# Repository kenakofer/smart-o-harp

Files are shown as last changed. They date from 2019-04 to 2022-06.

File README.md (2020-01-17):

## Summary

This site details an ongoing project to improve the chord selection mechanism on chromatic Autoharps/Chromaharps (hereafter called just "autoharps"). An arduino reads inputs from a keypad, computes the desired chord from the keypresses, and mechanically dampens the undesired strings.

It does **not** strum or pluck for the human, nor does it change chords without human input.

See [Motivations](#motivation) for why this project is useful.

See [Dampening Mechanism](#dampening-mechanism) for an for detailed analysis of dampening mechanism possibilities.

See [Avoiding harmonic nodes](#avoiding-harmonic-nodes) on the importance of considering harmonics when experimenting.

See [Keypad → Notes logic](#keypad--notes-logic) for more discussion than you wanted about sensible chord setups.

See [Wiring and Components](#wiring-and-components) to see how and with what it can be constructed.

--------

## Motivation
#### Autoharps are limited in number/variety of chords

Most autoharps have between 12 and 21 chord bars, with the ability to play in only some of the 12 musical keys. The chords available are usually major chords, minor chords, major-minor 7 chords, and sometimes a diminished chord.

Thinking just about these 4 types of chords, the maximal manual autoharp can play 21 of them, out of the `12*4=48` possible.

Stepping out of the chord bar paradigm can allow more flexibility.

#### Ergonomics of chord layouts can only go so far, and are not always key agnostic

The best layout I've found with 21 bars is to have each column be of the form (from farthest reach with the left hard to closest): `(Am, C, A7)`. Successive columns just walk this around the circle of fifths. This makes playing most major and minor songs in 5 key signatures ergonomic and *key agnostic* (transposing a song is as simple as shifting your chording hand over). Still, one of several flaws with this layout: When one wants the major/minor version of the minor/major chord, it's a wide reach that may go off the harp.

Stepping out of the 1 button = 1 chord paradigm can allow more flexibility.

#### Playing autoharps for long periods can cause cramping, arthritis, or other joint pain in the chording hand.

Depending on how well tuned the harp is and how the hand is positioned, this may be more or less of an issue. I don't play for more than an hour at a time, due to cramping.

Stepping out of the finger-force dampening paradigm etc.

----------

## Dampening mechanism

3 possibilities for this:

#### One solenoid per string

This is my current pursuit. Every string has a small solenoid positioned so that the unpowered state is dampening the string. When powered, the dampener lifts up, allowing that string to sound. The arduino controls the 30-40 solenoids individually, allowing more flexibility than the other two solutions. Cheap solenoids will cost around $1. The batteries I've tried cannot deliver the amps needed, so I'm trying a 12V, 5A laptop charger for now.

**Construction summary**: From a autoharp with exposed chord bars. Remove all bars except for one. Stretch the springs holding that bar so that the bar stays high under more force. Super glue solenoids to the sides of the bar such that the solenoids head is just short of touching the string it should dampen. Padding can then be glued to the head of the solenoid so that the resting state dampens the string effectively. Alternate placing solenoids on each side of the bar to give them enough lateral space.

**Considerations**: Size, shape, material of the dampening pads. Force of dampening. Lower notes' pads need more contact with the string to effectively dampen.

**Pros**: String by string flexibility for chord building, simple construction

**Cons**: Raised solenoids (undampened strings) draw current while remaining raised (one of my tiny $1 solenoids needs at least 70 mA to start lifting, and will continue to draw that while raised).

**Edit 01/13/2020**: On the second build iteration, I found solutions to the energy usage issues.

First, using a [voltage regulator](https://www.amazon.com/DROK-Converter-5-3V-32V-Regulator-Transformer/dp/B078Q1624B/), I was able to reduce the voltage to 9.5 or 10 volts, which reduces current through each solenoid. Each solenoid now needs about 140mA to raise.

Second, one of the solenoids only needs a tiny fraction of that power to stay raised, so the arduino can regulate down the power after a short time, greatly reducing energy costs.

This was a big problem to solve: It makes the prospect of raising all solenoids at once manageable, battery solutions are far more feasible, and the solenoids and components don't get super hot anymore!

#### Depress single-note bars with motor push

This is the second simplest solution. There are 12 "chord" bars, but their felts are cut so that one dampens only the `C`s, one dampens only the `C#`s, etc. Now to form an arbitrary chord, press down the set of bars that correspond to the pitch classes you **don't** want in the chord. Each depression will probably require more force than small solenoids can probably supply, so higher torque stepper motors may be better.

**Construction summary**: From an autoharp with exposed chord bars, take 12 bars and cut their felts to only dampen one pitch class. Replace them in a way to avoid damping on harmonic nodes. Get 12 high torque stepper motors with arms that swivel to straight down (to depress a bar). Mount them above the bars somehow, taking into account their difficult dimensions and the point of downward force on the bar relative to the strings being dampened. Given my lack of construction experience, this last task was too daunting for me.

**Considerations**: Force of dampening. Avoiding harmonic nodes.

**Pros**: Minimal power usage when not changing chords. May be cheaper than the solenoids if done effectively.

**Cons**: Complicated mounting that occupies space in front of chord bars, which may get in the way of the strumming hand.

#### Depress single-note bars with down pulling strings

I only mention this because I seriously tried making it work for a bit. Wouldn't recommend it.

Like the above in terms of the single note bars. For each bar: Tie a string to each end, run it straight downward and around a pivot point, then pull on both ends to depress the bar. Use a motor head to pull the strings taut to dampen a note.

**Considerations**: Allowing the motors to do no work when not changing chords. Motors need to have some torque.

**Pros**: The complicated mounting of the previous can be relocated somewhere less invasive (inside the autoharp body would be really interesting.

**Cons**: Starting to get quite complicated.

--------

## Avoiding harmonic nodes

See the [Wikipedia article](https://en.wikipedia.org/wiki/Harmonic) if you don't know what a harmonic node is. To experience it, place your finger or an eraser exactly halfway along a string, and pluck the string. An octave above the string's note will resonate. Slide along the string to find other points where the string will still sound.

That point on the string is a harmonic node, and is a poor location for a felt to dampen sound. There are other harmonic nodes at `(1/3, 2/3, 1/4, 3/4, 1/5, 2/5, ...)` etc. (all the rational numbers between 0 and 1). As the denominator gets bigger, it matters less in this context.

Whenever we mess with positions of bars and felts on the autoharp, we need to keep this consideration a priority to minimize extraneous noise while strumming. Consider marking all the harmonic nodes on the strings (e.g. with a red marker) before deciding on bar/felt placements that avoid those spots.

-------------

## Keypad &rarr; Notes logic

***Edit 01/13/2020***: If you don't care about motivations and thought processes, skip all this (very interesting) stuff past self wrote. I'll cover my current favorite keypad layout in [On Second Construction](#on-second-construction). That said, I still basically agree with all of this, past self just overlooked a few possibilities and didn't have enough buttons to press.

This project has the opportunity for a very consistent, learnable, ergonomic, key agnostic chord control mechanism. Optimizing for all these is a real puzzle, and different musicians will have different opinions and desires in this area.

Thankfully, the code on the arduino is far more easily changed than the mechanics of the construction, so we don't have to build a new autoharp if we forget a chord.

In this section, there will be tension between 1) incorporating more buttons/controls/physical complexity into the design, so that the amount of interaction needed to change to arbitrary chords is minimized, and 2) having fewer buttons/controls, so that the size/cost/physical complexity is minimized, but more interaction is needed to specify arbitrary chords. Each person probably has their own balance, but I lean more toward the fewer buttons/controls because I'm bad at electronics.

#### Music Theory Considerations for important triads

In a major key, here are the roman numeral chords I want easy access to, in decreasing order of importance: `(I, V(7), IV, vi, ii, II(7), iii, III(7), vii°, VI, VIIb, ...)`  I have high uncertainty after halfway through that list.

Similarly, in a minor key (using the roman numeral `vi` as the tonic chord for consistency): `(vi, iii, III(7), ii, V(7), I, IV, ...)` I have high enough uncertainty that I won't try to add more.

Songs with the richest harmonies have both minor and major progressions in them, so it behooves us to not only make the system key agnostic, but also *tonality agnostic* (a term I just made up: a song that starts major and then goes minor or vice versa shouldn't throw us for a loop).

The first 7 elements of each list have 6 in common, which (probably due to some arcane property of (meta-)music-theory) are also six-in-a-row around the circle of fifths: `(IV, I, V, ii, vi, iii)`.

Or, arranging them in rows as autoharpists typically do:

| | | |
| --- | --- | --- |
| IV  | I | V |
| ii  | vi  | iii |

This seems like an optimal arrangement of 6 buttons for playing diatonically, to be key and tonality agnostic. I'll treat these 6 chords as the core chords, which should be accessible through a single button press.

To actually make it key agnostic though, there needs to be a way to play in more than one key.

**Fixed chord root buttons**: We could do this with static buttons by having 24 buttons that we could arrange in 2 literal circles of fifths. The circles could be one inside the other, and then we literally have a circle of fifths as a control board:

major minor circle of fifths

24 buttons feels like a lot, but it gives us every major/minor triad, and it could make for a really attractive circular keypad, which could rotate to "switch" keys, and have modifier keys inside or outside the main circle. You would have to construct this yourself, as I can't find such a circular keypad online, even just for one row.

If your thumb is used to joysticks, another idea is to map the sectors of a joystick's movement to the circle of fifths. The lack of tactile feedback on the boundaries between chords, or the small 30&deg; sectors might be issues.

**Dynamic chord root buttons**: We can try to use program state to do it with fewer buttons: 6 buttons could code for `(IV, I, V, ii, vi, iii)` as in the table above, and 2 buttons could be used to change our key. Each button can change the key one direction or another around the circle of fifths. This has the disadvantage of not being able to jump to some arbitrary chord root outside the key: `VIIb` and `VIb` come to mind as somewhat common examples. And the chord `vii°` is entirely in the key and we can't reach it either.

The biggest problem is that the II and III chords aren't there. Adding another row can fix that, and also gives us all of the first 7 most important chords in major and minor from above:

| | | |
| --- | --- | --- |
| IV  | I | V |
| ii  | vi  | iii |
| II  | VI  | III |

This third row looks a little redundant next to the second row; especially if the "Swapping major/minor triad" modifier below is convenient to use.

#### Music Theory considerations for chord modifiers

We can expand the possibilities of these chords with modifiers. A modifier is a way to add or modify the notes in the 24 basic triads. Ideally, several modifiers could be added to one triad without much hassle. Each player will probably have a different preference for how these are arranged and which are included, or may even desire to change layouts between songs.

Here's my list of modifiers in decreasing order of importance and increasing order of my excitement: Adding a minor seventh, switching major/minor to minor/major triad respectively, diminishing the chord, sus4-ing the chord (!!), adding a major seventh to the chord (!!!), augmenting the chord (!!!!). There could be add2, add6, 9, 11, 13 stuff as well.

**Adding sevenths**: The major point of contention with having a `+7` modifier button is whether that 7 should be major or minor or context dependent. Chords with a major 7th above the root are rare, and seldom used outside of jazz. [Mechanical autoharps aren't great for jazz](http://jazzmando.com/new/archives/001511.shtml) (Only view if you aren't easily offended), and the possibility for major sevenths would help.

It isn't usually possible to predict the presence of major sevenths from the key signature, and chord sheets are explicit about when the 7 is major: `FM7` or `Fmaj7`. For this reason, it seems most best to use two separate modifiers: A `+min7` button that is in very easy reach for frequent use, and a `+maj7` button if the player wants it.

Alternatively, consider that a single button could be double tapped to get a different behavior, e.g. `+7` once for `+min7` and twice for `+maj7`.

**Swapping major/minor triads**: A `ii` becomes a `II`. A `iii` becomes a `III`. A common progression at the end of songs: `(I - iv - I)`. The `IV` and `V` in a major key get swapped out with their parallel minor counterparts for a more edgy harmony. The [Picardy third](https://en.wikipedia.org/wiki/Picardy_third) makes the last chord of a minor song (un)expectedly major.

Though a minor button and a major button separately are simpler to understand, the minor button would only be useful on major chords, and the major button only on minor chords. Combining them into a single button saves a button for something else.

**Diminished chords**: Three chords of interest: a [diminished triad](https://en.wikipedia.org/wiki/Diminished_triad) (3 notes with minor thirds between them), [fully diminished seventh chord] (https://en.wikipedia.org/wiki/Diminished_seventh_chord) (4 notes with minor thirds between them), and [half-diminished seventh chord](https://en.wikipedia.org/wiki/Half-diminished_seventh_chord) (a diminished triad with a minor seventh on top). The logic I've used thus far does not fit diminished chords well: We don't have `vii°` the most common diminished triad in our base triads; if we did, we still don't have a modifier to add a minor sixth to the chord for the fully diminished seventh. The most comprehensible solution is simply to add a modifier for each variation.

There are a few inelegant hacks we can use if we don't want to add so many buttons for these relatively rare chords. We could add one modifier button, a `dim` button, but have the button work in coordination with our `V` triad to produce the `vii°`. Why `V`? The diminished triad has a (dominant function)[https://en.wikipedia.org/wiki/Dominant_(music)] just like the `V`, and a `V7` can be thought of as a `vii°` with an added fifth scale degree.

We can co-opt other buttons that will not be much use in diminished chords, such as the `+maj7`, to be a `+min6` for the fully diminished chord. We can use the `+min7` as is to produce a half-diminished chord. Each of these chords would require 3 button presses: the `V`, the `dim`, and whichever `+7` button.

**Augmented chords**: These are a piece of proverbial cake relative to the diminished chords. An [augmented triad](https://en.wikipedia.org/wiki/Augmented_triad) is 3 notes separated by major thirds. Ignoring enharmonics (as I do) there are only 3 different augmented chords. So throw on an `aug` button, hit it with `I` or `iii` and you'll get the same effect. The `+7` modifiers are still there if you want to play a really exotic chord.

**Sus4 chords**: In a [sus4 chord](https://en.wikipedia.org/wiki/Suspended_chord) the 3rd is removed and a perfect 4th added. Pretty straightforward unless you want to hack together a more general system to get `sus2` without extra buttons, but I'm cool with just a `sus4` for now.

**You get the idea**: Other modifier ideas: removing the third to make open fifths, removing third and fifth to make octaves (yawn). "Scale" modifiers could be used for allowing playing any notes inside the scale by damping the ones outside the scale. Diatonic scale, pentatonic scale, various minor scales, or other less common scales.

#### Misc. operator buttons

**Left/Right around the circle of fifths**: 2 buttons, `mod5` and `mod4` to allow the instrument to change keys in two directions: `V` becomes `I`; and `IV` becomes `I`. Modulating by minor thirds might also be useful to go quickly between parallel major/minor keys.

**Previous chord**: There are frequently times when you are walking a melody up a scale and have to go back and forth between passing chords. Having a `prev` button to go to the chord just before the one currently playing could save 1 or 2 key presses depending on how complicated the chords are.

#### Keypress timing considerations

Timing is very important and has not yet been discussed. Some keypads do not support detecting multiple keys pressed at the same time, so combinations of keys pressed to produce a chord cannot happen at once. We will call this a _sequential_ keypad system. Many more keypads have, at least in their hardware, the ability to correctly detect certain simultaneous keypresses, but not others. We'll call a system that can detect some number of simultaneous keypresses correctly a _simultaneous_ keypad system. We'll start with thinking sequentially for simplicity's sake.

#### Sequential principles

Most of the time when you press the `IV` button, you just want to play that chord as is. But suppose one time in the middle of a song it's a minor `iv` chord, requiring the major/minor modifier plus the `IV` button. Thinking sequentially, one button press has to come before the other.

If the `IV` is first, the arduino can either 1) wait for more input, or 2) immediately make the chord available with possibly the wrong tonality.

If the `maj/min` is first, the arduino can either 3) wait for more input, or 4) immediately change the current chord to the opposite tonality.

Of these 4 scenarios, I like 3 best. Immediate changes mean the instrument will be in states of the wrong tonality. If the arduino is to wait for something, it's best that the "something" be definite. We've talked about the 6 fundamental triad controls, and one reason they are so fundamental is that they are the common element, and thus can safely be the element that actuates the changing of the chords in one quick motion.

Say we're in C major, and we want to play `E7`, which is `III7`. So the order of the sequential presses would be `maj/min`, `+m7`, `iii`. Only pressing the final button would cause the dampened strings to change. Not gonna lie: this sounds painful given how often I use `III7`.

#### Sequential layout ideas

Given the above, here are some of my ideas for "good" sequential keypad layouts. Any of these could have part or all of it rotated 90&deg; to better fit under the fingers.

**12 button sequential keypad A (fast and simple):**

| | | |
| --- | --- | --- |
| IV  | I | V |
| ii  | vi  | iii |
| II7 | VI7 | III7|
| mod4|+min7| mod5|

This layout should play melodies quickly and efficiently. The presence of the third triad row (with 7s already added because of their nearly universal use on secondary dominants) allows us to leave out `maj/min` modifier. We can play most chords with a single keypress, with the exception of the `V7` (this is a real downer). Even with just these 12 buttons, the player can play in all 12 key signatures, major and minor, with the most common chords, have minor chords with minor sevenths, major sevenths if you use a double-tap logic, and modulate keys mid song without fuss. 

Some players might like swapping out the `+min7` for a `V7` button, or have the double tap behavior provide the `V7`, or some variation on that.

**12 button sequential keypad B (slower and deeper):**

| | | |
| --- | --- | --- |
| IV  | I | V |
| ii  | vi  | iii |
|+min7|maj/min|sus4|
| mod4|prev | mod5|

We remove our convenience row of chords to add more cool modifiers to show off with. Double taps would open open up more possibilities `+min7`  &rarr; `+maj7`; `maj/min` &rarr; `dim`; `sus4`  &rarr; `sus2`. But here the secondary dominants with sevenths require 3 presses. This could be fine for chording and slower melodies, but not faster ones. The `prev` button recovers some speed between alternating chords.

#### Simultaneous principles in row, column keypads

The possibility of pressing multiple keys at the same time allows for faster fingering of chords with modifiers, but introduces complexities of hardware and timing. For a better introduction to these issues on a typical computer keyboard, [see here](https://en.wikipedia.org/wiki/Rollover_(key)).

**No ground pin**: It's common for keypads to be wired such that each row and column corresponds to a pin, such that pressing the button in the first row and first column connects the first row pin (`row1`) to the first column pin (`col1`). Suppose that the button in the first row, second column is also pressed. then `row1`, `col1`, and `col2` are all connected to each other.

Keypad backside wiring

But the arduino's logic is in reverse: (Ex. 1) If it sees that `row2`, `col3`, and `col4` are connected to each other, can it know for certain what buttons are pressed? In this case, yes, because a button press is always at the intersection of a row and column, and a row or column pin can't be in the connected list without having a pressed button. We can extend this logic to say that any number of keypresses in any single row or in any single column are always safely distinguishable.

(Ex. 2) If `row1` and `col1` are connected, and `row2` and `col2` are separately connected, the arduino still knows the exact two buttons that are pressed. This, along with the first example, shows that any two simultaneous keypresses are distinguishable.

Certain combinations of 3 simultaneous keypresses introduce ambiguity. (Ex. 3) If ever there is a pressed button (e.g. `row1, col1`) who has another pressed button buddy in their row (`row1, col2`), and also a pressed button buddy in their column (`row2, col1`), then all the arduino sees is a group of 4 connected pins: `row1`, `row2`, `col1`, `col2`. Some combination of 3 or 4 of these were pressed, but there's no way to know which. 

However, ambiguity is not necessarily a deal-breaker: as long as the arduino has a sensible default for how to interpret specific situations of ambiguity, it can use that default. We just want to avoid designing a system that allows two useful "button signatures" to have the same "pin signature" from the arduino's perspective.

**With ground pin**: My keypad is weird in that it has a pin that connects to every button, which I'll call the `ground`. So pressing the top left button connects `row1`, `col1`, and `ground`. So Ex. 2 isn't a possibility, because all button presses connect the entire set of row and column pins involved. So the only unambiguous button presses are, as descibed in Ex. 1, within a single column or within a single row. The same note about ambiguity applies.

I'm honestly not sure where I got this keypad, or why I would want this `ground` pin when it seems to only decrease the functionality.

**Regardless**, it is safe for us to make plans for simultaneous keypresses in a single row or column. This limitation still allows quite a few possibilities, but makes simultaneous modifier keys, like a `+min7` difficult to put somewhere that is usable by all the relevant chords. As a result, I'll try to avoid having modifier keys at all.

**12 button simultaneous keypad (Bear With Me edition):**

This will get kind of complicated to diagram now. It's better to have lots of choices IMHO, but I realize many will disagree with me. Note that "2 buttons to the left" will sometimes mean wrapping back around to the right side.

**Interpretation:** Default chord (chord when button to the left is also pressed) (chord when the 2 buttons to the left are both pressed)

| | | | |
| --- | --- | --- | --- |
|  VIIb (vii°) (vii°7) | IV (IV7) (IVmaj7) | I (I7) (Imaj7)  | V (V7) (Vmaj7) |
| v (iv) (i)  | ii (II7) (ii7) | vi (VI7) (vi7) | iii (III7) (iii7) |
| mod4 | prev | +sus4 | mod5 |

First off, I sincerely apologize for the first column, you may ignore it as you are picking up the pattern of the rest of the table. 

Pressing a bunch of buttons in a row are interpreted as a modifier on the rightmost of the buttons pressed (wrapping from left to right is important, e.g. to get the `vii°` one would press `VIIb` and `V`). This mostly serves to add various sevenths to chords, and differs between the major and minor triads.

**Major**: When 1 button to the left is pressed, it does `+min7`. When 2 buttons are pressed, it `+maj7`s the chord.

**Minor**: When 1 button to the left is pressed, it majors it and does `+min7`. When 2 buttons are pressed, it just `+min7`s the chord. I didn't use `+maj7` because that isn't as much used on minor chords.

And the first column just throws in all the things I would be sad not to have, in a vaguely circle-of-fifths-y way. This layout throws easy comprehension out the window in favor of packing in the options in an ergonomic manner (Imagine alternating between fingerings for `I` and `V7`, just by lifting a single finger, or doing the same between `III7` and `vi`).

Note that on a grounded pin keypad, the `+sus4` introduces ambiguity when pressed simultaneously with, say, `V`. It connects pins `row3`, `col3`, `row1`, and `col4`. However, if we are content with only using `+sus4` with a single other button press, and not using the other buttons in the 3rd row with the triad buttons, we can have the arduino interpret this ambiguity predictably as using the `+sus4` with whichever button is diagonal to it. No-ground-pin keypads don't need to worry about this.

I'm not sure how useful the `prev` button will be in this layout, because most back-and-forth passing chords are pretty easy to go between already. I add it here mostly because I don't know what else to put in that space. I can't have another typical modifier due to the paragraph above. I could have a parallel minor modifier that is only used with the `mod4` and `mod5` buttons to change key up or down by a minor 3rd easily. Or I could put another chord there, like the `VIb`.

## On Second Construction

This section is written much later. On the second construction attempt, I solved a lot of major issues.

I started over building because the first build was cludgy and bad in its
unfinished state. Here are the major changes in the second construction, in
the software:

 - Using 16 button keypad (4 column, 4 row pins, no weird ground pin
 this time ;) This allows:
 - Different button reading strategy: Use two dimensional array of
 button states rather than row and column states. This allows a lot more
 keypresses without ambiguity.
 - Keymapping to chords substantially rethought. Now it doesn't use ANY
 simultaneous keypresses, but considers some keys as "modifiers" which
 don't do anything when pressed on their own, and "actuators" (maybe
 find better name?) which when pressed immediately actuate a chord with
 whatever modifiers are down. See the big comment in the code for the
 layout.
 - The above means that we were able to get rid of the `buffer_chord`
 system entirely! :celebrate:
 - Chords can now have up to 5 notes to allow for things like Dominant 9
 chords. No reason it couldn't be more.
 - Major power reduction by using pin 10 on the arduino to change
 current flowing to the solenoids. The solenoids need lots more power to
 pop up than they need to stay up, so every chord change starts at
 `FULL_POWER` then drops power usage considerably to `LOW_POWER` after
 `TICKS_AT_FULL_POWER` ticks.
 - Pasted in the function `setPwmFrequency` to use on pin 10, because
 the default, slower frequencies cause audible hums during `LOW_POWER`

Major changes in the hardware that weren't mentioned in the software:

 - I'm now soldering female header pin connectors rather than the components themselves into the soldering board. If I fry another Arduino Nano or break a keypad it will be a trivial swap-out rather than a solder-mess project-killer.
 - Similarly, on each solenoid, I'm putting a jumper cable head on one of the wires. This way, it can be plugged in rather than soldered in. Same logic as above, and flexibility of rewiring on the fly if the autoharp strings are tuned to different pitches.
 - I'm now using a [voltage regulator](https://www.amazon.com/DROK-Converter-5-3V-32V-Regulator-Transformer/dp/B078Q1624B/), which helps me fiddle with and monitor power better. It might not be necessary in the long run, but for a prototype it is _incredibly_ handy to simply bump the voltage up or down.
 - I'm not trying to incororate LEDs this time around. Simpler design, more in my pay grade.

### Most recent keypad layout (4x4 buttons)

My new keypad's hardware doesn't have ambiguity unless 3 or more button presses are at the corners of a rectangular area. This allows some clever setup of held (not simultaneous press!) modifier keys. Getting rid of simultinaety is huge I think.

**Single press with single modifier**

| | | | |
| --- | --- | --- | --- |
| VIIb | IV | I | V |
| ii | vi | iii | vii° |
| _Make Do_ | _Sus2_ | _Sus4_ | _Maj/Min_ |
| _mM7_ | _MM7_ | _mm7_ | _Mm7_ |

**Single press with double modifier in vertical stacks**

| | | | |
| --- | --- | --- | --- |
| VIIb | IV | I | V |
| ii | vi | iii | vii° |
| _Dim_ | _Aug_ | _Dim7_ | _1/2 Dim 7_ |
| _(^^^)_ | _(^^^)_ | _(^^^)_ | _(^^^)_ |

Note that:

 - The arrows _(^^^)_ mean that both modifiers must be pressed for the listed modifier to apply. Still, nothing will actuate until a chord button is pressed.
 - Because these modifiers are vertically stacked, it is impossible for a single chord button to form a rectangular area, so hardware ambiguity is avoided.

**Single press with double modifier in diagonal combinations**

| | | | |
| --- | --- | --- | --- |
| VIIb | IV | I | V |
| ii | vi | iii | vii° |
| | | _Dom9_ | |
|  |  |  | _(Dom9)_ |

Note that:

 - I'm not sure how well these combos will work ergonomically, so I'm only trying one for now. _Dom9_ means Root, M3, P5, m7, M9(M2).
 - Once again, these diagonal combinations avoid hardware ambiguity when one of the chord buttons is pressed

**Horizontal Double modifier as chord button:**

| | | | |
| --- | --- | --- | --- |
| VIIb | IV | I | V |
| ii | vi | iii | vii° |
| | | VIb | (<<<) |
|  |  | IIIb | (<<<) |

 - These horizontally aligned modifiers would NOT work unambiguously with all chord buttons (If the `I` were pressed, it would look like `V` was also pressed), so it seems reasonable to actually make the modifiers actuate in combination with each other. This means that these particular chords can't have modifiers applied to them to make, for example, a VIb seventh chord.
 - Not all slots are used, because most other chords we really want to be able to add other modifiers

 I'll update the Wiring and Components section at some point, it's outdated for now

--------

## Outdated Wiring and Components

3 main topics here, which others have covered pretty well already so I don't need to. Click the links to read more.

1. [8-bit shift registers](https://www.arduino.cc/en/tutorial/ShiftOut): Getting the (at least) 12 outputs necessary to control 12 systems of solenoids independently, without using up all the arduino's pins.

2. [Driving solenoids with an arduino](https://core-electronics.com.au/tutorials/solenoid-control-with-arduino.html): Except that we will drive the solenoids and the arduino off the same power source, so maybe this isn't super relevant.

3. [Keypad input method](https://www.instructables.com/id/Arduino-Button-Tutorial/): having the arduino read in button presses. This is basic input/output stuff, and the linked tutorial is excellent for looking at a single case. I've covered the specific convoluted logic of my keypad already.

Here's my breadboard setup all laid out. This is diagram version 2, using the nano and fixing some wire placement issues from the first version. 

**Disclaimer**: I'm not great at electronics as I write this. I fried several components on my way to what I hope is a safe, working design.

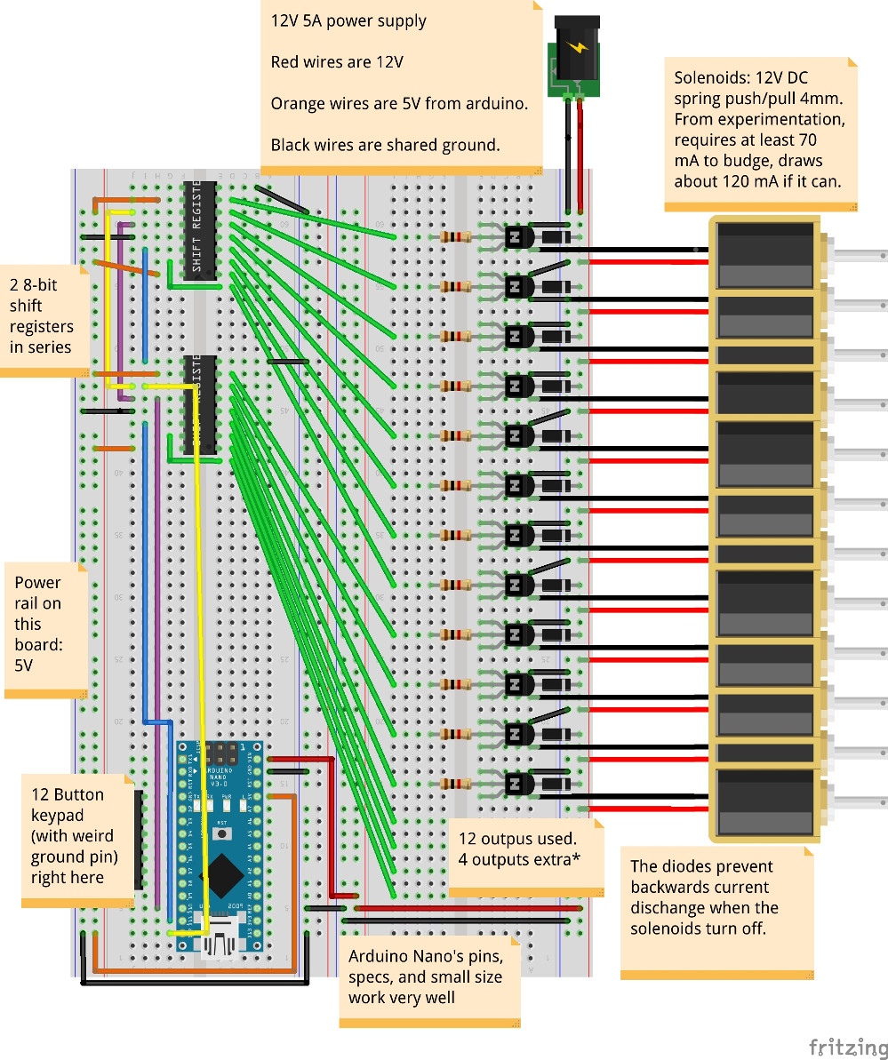
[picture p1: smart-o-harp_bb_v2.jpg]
Breadboard Fritzing diagram


#### Diagram notes

For every one solenoid shown in the diagram, there will be upwards of 4 solenoids wired in parallel with it, so that all the `C` solenoids share a transistor, and so do the `C#` solenoids etc.

The 4 "extra" outputs could be used to wire the 4 bottom strings of the autoharp individually, so that you can have, for example, the `G7` chord not include the bottom `F`, but still include all the other `F`s.

Other than using 12V to power the arduino on the Vin pin, keep the 12V as far away from the arduino as possible. I fried one Nano by momentarily bridging a connection from 12V to the Nano's 5V pin.

#### Outdated Components list

 * I used [this SB1660 busboard](https://www.amazon.com/gp/product/B00LLOOA0U) for soldering a semi-permanent prototype.
 * Arduino Nano
 * 12V, 5A power supply
 * 2 x 74HC595 chip
 * 12-16 x 1kΩ resistors
 * ~36 x [12V 120mA spring push pull solenoids](https://www.ebay.com/itm/12V-DC-Suction-Micro-Electromagnet-Spring-Push-Pull-Type-Rod-Solenoid-Magnet-4mm/153089629798) (You need one for each autoharp string.)
 * 12-16 x 2N2222 (NPN, BJT) transistors
 * 12-16 x 1N4001 diodes

----

## Code

[Here's the code](https://github.com/kenanbit/smart-o-harp/blob/master/code/code.ino). It's fairly straightforward.

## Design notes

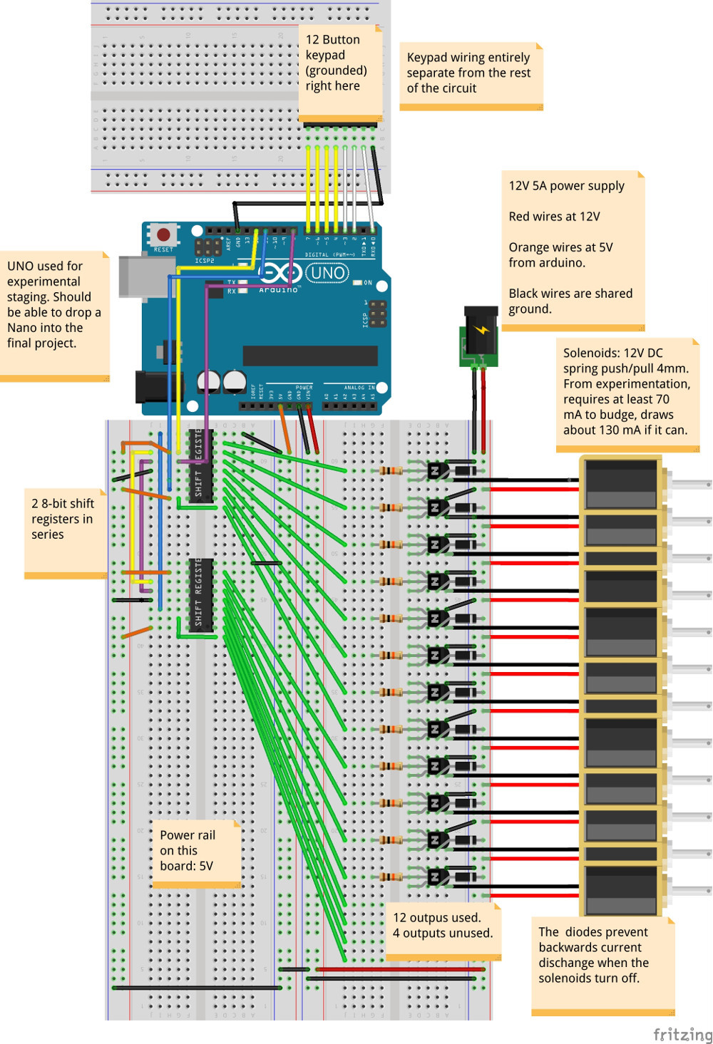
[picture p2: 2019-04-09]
smart-o-harp_bb_v1.jpg

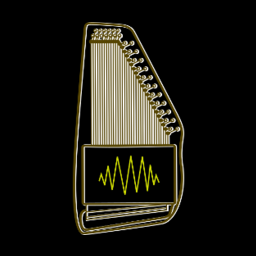
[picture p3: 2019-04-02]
android-chrome-256x256.png

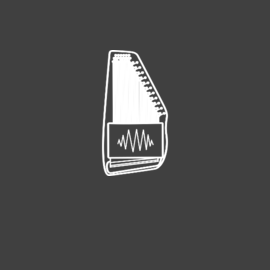
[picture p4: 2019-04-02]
mstile-150x150.png

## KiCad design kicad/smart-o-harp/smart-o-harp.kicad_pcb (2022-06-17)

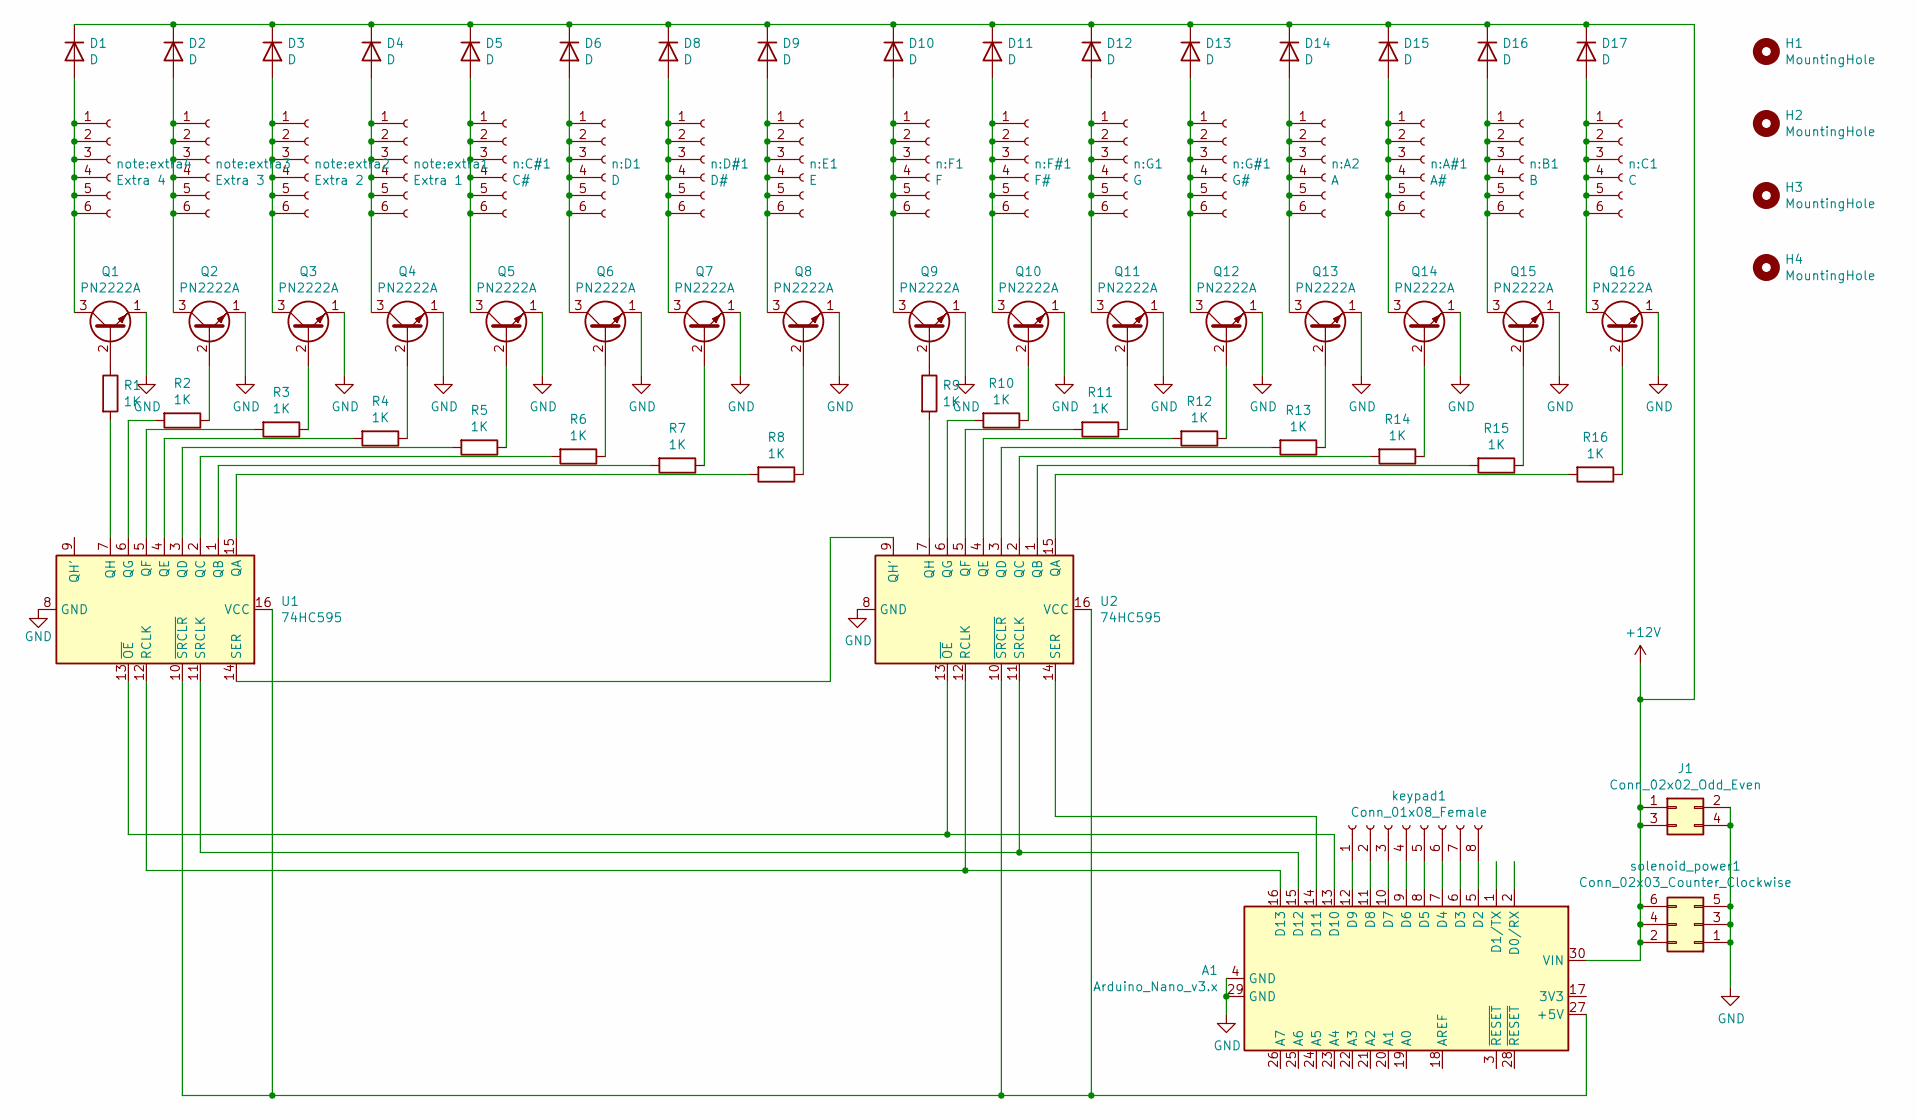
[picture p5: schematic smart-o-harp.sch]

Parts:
A1: Arduino_Nano_v3.x; Arduino_Nano
D1, D2, D3, D4, D5, D6, D8, D9, D10, D11, D12, D13, D14, D15, D16, D17: D; D_A-405_P5.08mm_Vertical_AnodeUp
H1, H2, H3, H4: MountingHole; MountingHole_3.2mm_M3
J1: Conn_02x02_Odd_Even; PinHeader_2x02_P2.54mm_Vertical
Q1, Q2, Q3, Q4, Q5, Q6, Q7, Q8, Q9, Q10, Q11, Q12, Q13, Q14, Q15, Q16: PN2222A; TO-92_Wide
R1, R2, R3, R4, R5, R6, R7, R8, R9, R10, R11, R12, R13, R14, R15, R16: 1K; R_Axial_DIN0204_L3.6mm_D1.6mm_P5.08mm_Horizontal
U1, U2: 74HC595; DIP-16_W7.62mm
keypad1: Conn_01x08_Female; PinHeader_1x08_P2.54mm_Vertical
n:A2: A; PinHeader_1x06_P2.54mm_Vertical
n:A#1: A#; PinHeader_1x06_P2.54mm_Vertical
n:B1: B; PinHeader_1x06_P2.54mm_Vertical
n:C1: C; PinHeader_1x06_P2.54mm_Vertical
n:C#1: C#; PinHeader_1x06_P2.54mm_Vertical
n:D1: D; PinHeader_1x06_P2.54mm_Vertical
n:D#1: D#; PinHeader_1x06_P2.54mm_Vertical
n:E1: E; PinHeader_1x06_P2.54mm_Vertical
n:F1: F; PinHeader_1x06_P2.54mm_Vertical
n:F#1: F#; PinHeader_1x06_P2.54mm_Vertical
n:G1: G; PinHeader_1x06_P2.54mm_Vertical
n:G#1: G#; PinHeader_1x06_P2.54mm_Vertical
note:extra1: Extra 1; PinHeader_1x06_P2.54mm_Vertical
note:extra2: Extra 2; PinHeader_1x06_P2.54mm_Vertical
note:extra3: Extra 3; PinHeader_1x06_P2.54mm_Vertical
note:extra4: Extra 4; PinHeader_1x06_P2.54mm_Vertical
solenoid_power1: Conn_02x03_Counter_Clockwise; PinHeader_2x03_P2.54mm_Vertical

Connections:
+12V: A1.30 (VIN), D1.1 (K), D2.1 (K), D3.1 (K), D4.1 (K), D5.1 (K), D6.1 (K), D8.1 (K), D9.1 (K), D10.1 (K), D11.1 (K), D12.1 (K), D13.1 (K), D14.1 (K), D15.1 (K), D16.1 (K), D17.1 (K), J1.1, J1.3, solenoid_power1.2, solenoid_power1.4, solenoid_power1.6
GND: A1.4 (GND), A1.29 (GND), J1.2, J1.4, Q1.1 (E), Q2.1 (E), Q3.1 (E), Q4.1 (E), Q5.1 (E), Q6.1 (E), Q7.1 (E), Q8.1 (E), Q9.1 (E), Q10.1 (E), Q11.1 (E), Q12.1 (E), Q13.1 (E), Q14.1 (E), Q15.1 (E), Q16.1 (E), U1.8 (GND), U2.8 (GND), solenoid_power1.1, solenoid_power1.3, solenoid_power1.5
unnamed: A1.5 (D2), keypad1.8
unnamed: A1.6 (D3), keypad1.7
unnamed: A1.7 (D4), keypad1.6
unnamed: A1.8 (D5), keypad1.5
unnamed: A1.9 (D6), keypad1.4
unnamed: A1.10 (D7), keypad1.3
unnamed: A1.11 (D8), keypad1.2
unnamed: A1.12 (D9), keypad1.1
unnamed: A1.13 (D10), U1.13 (~OE), U2.13 (~OE)
unnamed: A1.14 (D11), U2.14 (SER)
unnamed: A1.15 (D12), U1.11 (SRCLK), U2.11 (SRCLK)
unnamed: A1.16 (D13), U1.12 (RCLK), U2.12 (RCLK)
unnamed: A1.27 (+5V), U1.10 (~SRCLR), U1.16 (VCC), U2.10 (~SRCLR), U2.16 (VCC)
unnamed: D1.2 (A), Q1.3 (C), note:extra4.1, note:extra4.2, note:extra4.3, note:extra4.4, note:extra4.5, note:extra4.6
unnamed: D2.2 (A), Q2.3 (C), note:extra3.1, note:extra3.2, note:extra3.3, note:extra3.4, note:extra3.5, note:extra3.6
unnamed: D3.2 (A), Q3.3 (C), note:extra2.1, note:extra2.2, note:extra2.3, note:extra2.4, note:extra2.5, note:extra2.6
unnamed: D4.2 (A), Q4.3 (C), note:extra1.1, note:extra1.2, note:extra1.3, note:extra1.4, note:extra1.5, note:extra1.6
unnamed: D5.2 (A), Q5.3 (C), n:C#1.1, n:C#1.2, n:C#1.3, n:C#1.4, n:C#1.5, n:C#1.6
unnamed: D6.2 (A), Q6.3 (C), n:D1.1, n:D1.2, n:D1.3, n:D1.4, n:D1.5, n:D1.6
unnamed: D8.2 (A), Q7.3 (C), n:D#1.1, n:D#1.2, n:D#1.3, n:D#1.4, n:D#1.5, n:D#1.6
unnamed: D9.2 (A), Q8.3 (C), n:E1.1, n:E1.2, n:E1.3, n:E1.4, n:E1.5, n:E1.6
unnamed: D10.2 (A), Q9.3 (C), n:F1.1, n:F1.2, n:F1.3, n:F1.4, n:F1.5, n:F1.6
unnamed: D11.2 (A), Q10.3 (C), n:F#1.1, n:F#1.2, n:F#1.3, n:F#1.4, n:F#1.5, n:F#1.6
unnamed: D12.2 (A), Q11.3 (C), n:G1.1, n:G1.2, n:G1.3, n:G1.4, n:G1.5, n:G1.6
unnamed: D13.2 (A), Q12.3 (C), n:G#1.1, n:G#1.2, n:G#1.3, n:G#1.4, n:G#1.5, n:G#1.6
unnamed: D14.2 (A), Q13.3 (C), n:A2.1, n:A2.2, n:A2.3, n:A2.4, n:A2.5, n:A2.6
unnamed: D15.2 (A), Q14.3 (C), n:A#1.1, n:A#1.2, n:A#1.3, n:A#1.4, n:A#1.5, n:A#1.6
unnamed: D16.2 (A), Q15.3 (C), n:B1.1, n:B1.2, n:B1.3, n:B1.4, n:B1.5, n:B1.6
unnamed: D17.2 (A), Q16.3 (C), n:C1.1, n:C1.2, n:C1.3, n:C1.4, n:C1.5, n:C1.6
unnamed: Q1.2 (B), R1.1
unnamed: Q2.2 (B), R2.1
unnamed: Q3.2 (B), R3.1
unnamed: Q4.2 (B), R4.1
unnamed: Q5.2 (B), R5.1
unnamed: Q6.2 (B), R6.1
unnamed: Q7.2 (B), R7.1
unnamed: Q8.2 (B), R8.1
unnamed: Q9.2 (B), R9.1
unnamed: Q10.2 (B), R10.1
unnamed: Q11.2 (B), R11.1
unnamed: Q12.2 (B), R12.1
unnamed: Q13.2 (B), R13.1
unnamed: Q14.2 (B), R14.1
unnamed: Q15.2 (B), R15.1
unnamed: Q16.2 (B), R16.1
unnamed: R1.2, U1.7 (QH)
unnamed: R2.2, U1.6 (QG)
unnamed: R3.2, U1.5 (QF)
unnamed: R4.2, U1.4 (QE)
unnamed: R5.2, U1.3 (QD)
unnamed: R6.2, U1.2 (QC)
unnamed: R7.2, U1.1 (QB)
unnamed: R8.2, U1.15 (QA)
unnamed: R9.2, U2.7 (QH)
unnamed: R10.2, U2.6 (QG)
unnamed: R11.2, U2.5 (QF)
unnamed: R12.2, U2.4 (QE)
unnamed: R13.2, U2.3 (QD)
unnamed: R14.2, U2.2 (QC)
unnamed: R15.2, U2.1 (QB)
unnamed: R16.2, U2.15 (QA)
unnamed: U1.14 (SER), U2.9 (QH')

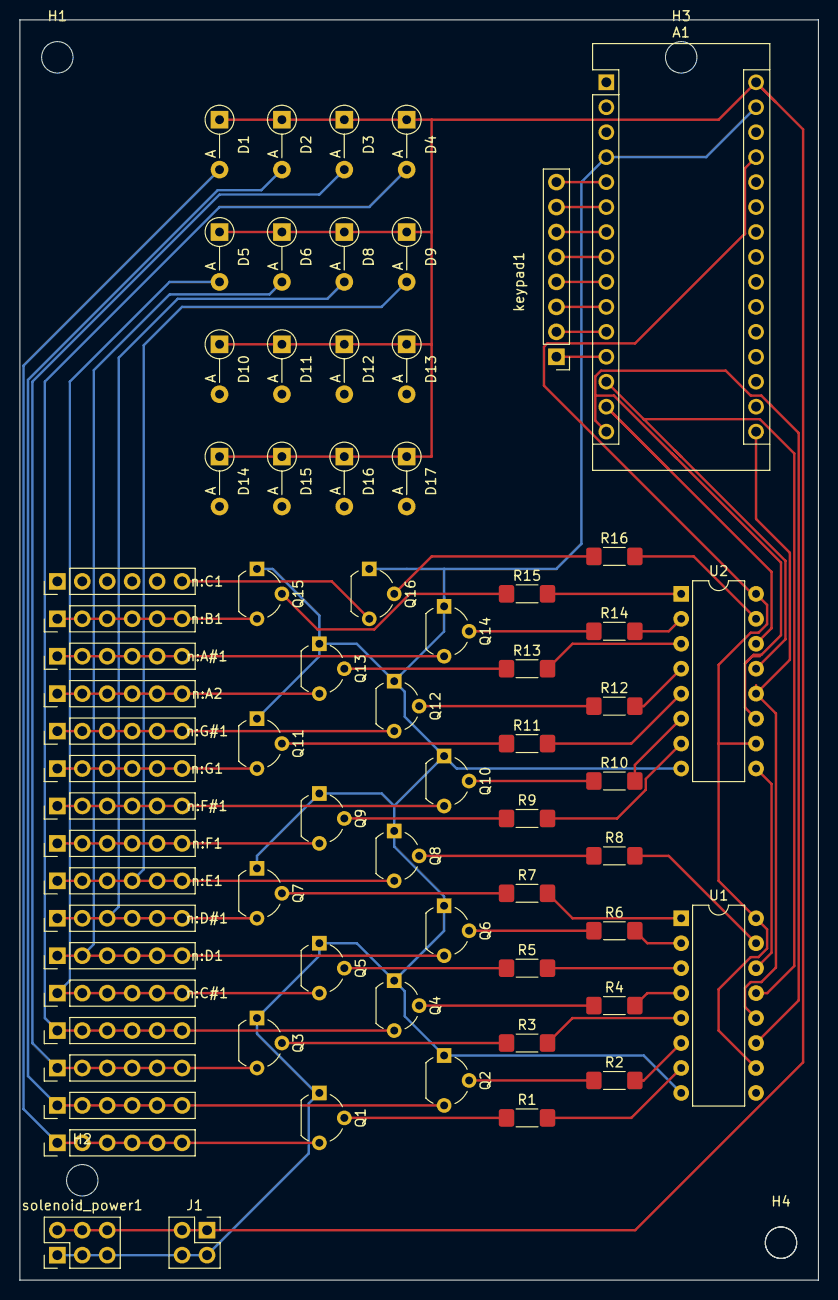
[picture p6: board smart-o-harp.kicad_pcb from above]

Board: 2 copper layers, 81.3 x 128.3 mm, 74 parts (0 on the bottom side), 64 nets.

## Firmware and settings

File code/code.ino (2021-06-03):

const int TICK_DURATION = 5; //How long (ms) between runs of the loop

const char *notes[] = {"C", "Db", "D", "Eb", "E", "F", "Gb", "G", "Ab", "A", "Bb", "B"};
const int CHORD_LENGTH = 5;

// -1 means no note. The other indices can be looked up in the notes[] array
// above, for each of these triads in the key of C. For example, a value of 2
// in the key of C would be D, but a value of 2 in the key of G would be A.
const int NONE[] = {-1, -1, -1, -1, -1};
const int IV[] = {5, 9, 0, -1, -1};
const int I[] = {0, 4, 7, -1, -1};
const int V[] = {7, 11, 2, -1, -1};
const int II[] = {2, 6, 9, -1, -1};
const int VI[] = {9, 1, 4, -1, -1};
const int III[] = {4, 8, 11, -1, -1};
const int VII[] = {11, 3, 6, -1, -1};
const int VIIb[] = {10, 2, 5, -1, -1};
const int VIb[] = {8, 0, 3, -1, -1};
const int IIIb[] = {3, 7, 10, -1, -1};
const int Isharp[] = {1, 5, 8, -1, -1};
const int IVsharp[] = {6, 10, 1, -1, -1};

const int NOTE_SOLENOID_ORDER[] = {0, 11, 10, 9, 8, 7, 6, 5, 4, 3, 2, 1}; // From closest to arduino to farthest away, what semitone scale degree is on the pin. 0 is C, 1 is Db, etc. as seen in notes[]

const int FULL_POWER = 0; // The PWM_POWER_PIN => OE pin duty cycle to get full power to the active solenoids. This means grounding the OE pin, letting the shift regitsers operate full-time
const int MID_POWER = 50; // By only having the 8-bit registers active some of the time, we use less power. Less power is needed to hold the solenoids in place.
const int LOW_POWER = 235; // This is the lowest level of power that can maybe hold the solenoids. Only used in opening all strings.
const int NO_POWER = 255; // Keeping the OE pin high disables the 8 bit shift registers
const int TICKS_AT_FULL_POWER = 10; // How long before decreasing power after chord change.

const int PWM_POWER_PIN = 10; // Available PWM pins (uno and nano): 3, 5, 6, 9, 10, 11
const int LATCH_PIN = 13;  //Pin connected to latch pin (ST_CP) of 74HC595
const int CLOCK_PIN = 12; //Pin connected to clock pin (SH_CP) of 74HC595
const int DATA_PIN = 11; //Pin connected to Data in (DS) of 74HC595

const int TICKS_BETWEEN_ONPRESS_ACTIONS = 4; // Ticks over which a key change combo, PREV keypress, or other toggle must NOT be pressed before another such change is allowed

const int COL_PIN_COUNT = 4;
const int COL_PIN_NUMBERS[] = { 9, 8, 7, 6 };

const int ROW_PIN_COUNT = 4;
const int ROW_PIN_NUMBERS[] = { 5, 4, 3, 2 };

const bool KEYPAD_FLIP_VERTICAL = false; // Set to true if the keypad is installed flipped vertically
const bool KEYPAD_FLIP_HORIZONTAL = false; // Set to true if the keypad is installed flipped horizontally

int current_key = 0; // The key the instrument starts in, with C being 0

int current_power = FULL_POWER; // can go up and down incrementally between ticks
int tick_counter = 0;  // Counts up with each loop();
int last_chord_change_tick = 0; // The tick at which the last chord change happened.
int last_onpress_action = 0; // The tick at which the last key change happened.
int current_chord[] = {-1, -1, -1, -1, -1}; // The chord actually actuated on the solenoids now or by the end of loop(). Starts as a nothing chord
int last_tick_chord[] = {-1, -1, -1, -1, -1}; // Last tick's current_chord. Used to tell if, in the current tick, we need to change the shift registers' states.
int prev_chord[] = {-1, -1, -1, -1, -1}; // The most recently actuated chord that is different from the current one.
bool auto_play = false; // When true, changing chords will bounce the new active solenoids on the strings, softly sounding the new chord.

int pin_states[COL_PIN_COUNT][ROW_PIN_COUNT];

bool is_same_chord(const int chord1[], const int chord2[]) {
    for (int i=0; i<CHORD_LENGTH; i++) {
        if (chord1[i] != chord2[i]) {
            return false;
        }
    }
    return true;
}

bool is_minor(const int chord[]) {
    return (chord[1] == (chord[0] + 3) % 12) && (chord[2] == (chord[0] + 7) % 12);
}

bool is_major(const int chord[]) {
    return (chord[1] == (chord[0] + 4) % 12) && (chord[2] == (chord[0] + 7) % 12);
}

void update_last_tick_chord() {
    for (int i=0; i<CHORD_LENGTH; i++) {
        last_tick_chord[i] = current_chord[i];
    }
}

void update_prev_chord() {
    for (int i=0; i<CHORD_LENGTH; i++) {
        prev_chord[i] = last_tick_chord[i];
    }
}

void actuate_current_chord() {
    // Get the byte representation of the chord's notes
    int bitsToSend = 0;
    for (int i=0; i<CHORD_LENGTH; i++) {
        if (current_chord[i] >= 0) {
          bitsToSend += 1<<NOTE_SOLENOID_ORDER[current_chord[i]];
          Serial.print("Adding ");
          Serial.println(1<<NOTE_SOLENOID_ORDER[current_chord[i]]);
        }
    }
    /*if (bitsToSend == 0){
      Serial.println("Will not actuate: Chord is NONE");
      return;
    }*/
    for (int n=0; n<CHORD_LENGTH; n++) {
      Serial.print(current_chord[n]);
      Serial.print(" ");
    }
    Serial.println();

    send_bits(bitsToSend);
}

void send_bits(const int bits) {
    byte A = bits & 0x00ff;
    byte B = (bits & 0xff00) >> 8;

    // Start the shift register listening
    digitalWrite(LATCH_PIN, LOW);
    // shift the bytes out, B to the first, A to the second:
    shiftOut(DATA_PIN, CLOCK_PIN, MSBFIRST, B);
    shiftOut(DATA_PIN, CLOCK_PIN, MSBFIRST, A);
    // Stop listening, turn on the outputs
    digitalWrite(LATCH_PIN, HIGH);
}

// Copy the specified triad into the current_chord
void set_current_chord_in_current_key(const int chord[]) {
    for (int i=0; i<CHORD_LENGTH; i++) {
        // Only change the note by key if it's a played note. Otherwise, it's
        // -1 and shouldn't be changed.
        if (chord[i] >= 0) {
            current_chord[i] = (chord[i] + current_key) % 12;
        } else {
            current_chord[i] = chord[i];
        }
    }
}

void set_current_chord(const int chord[]) {
    for (int i=0; i<CHORD_LENGTH; i++) {
            current_chord[i] = chord[i];
    }
}

// This function takes control for a (hopefully small) period of time. It doesn't really work, and should not be used in its current state.
void open_all_strings() {
    Serial.println("open_all_strings()");
    const int MICROSECOND_DELAY = 100;
    const int DELAYS_TO_RAISE = 400;
    const int LOW_POWER_INTERVAL = 8;
    const int ALL_BITS = (1<<13) - 1; // => 111 111 111 111 I think

    // Set to full power so communication goes correctly
    current_power = FULL_POWER;
    set_solenoid_power(current_power);

    // For each note needing to be opened
    for (int i=0; i<12; i++) {
        for (int count=0; count < DELAYS_TO_RAISE; count++) {
            // All pins get power this iteration
            if (count % LOW_POWER_INTERVAL == 0) {
                send_bits(ALL_BITS);
            } else {
                // Only the to-be-raised notes gets full power this time.
                send_bits(1<<i);
            }
            delayMicroseconds(MICROSECOND_DELAY);
        }
    }
    // Now all notes should be raised.
    // Leave all bits on, and LOW_POWER
    send_bits(ALL_BITS);
    current_power = LOW_POWER;
    set_solenoid_power(current_power);

    // Change both current chord and last_tick_chord to NONE so it isn't overwritten.
    set_current_chord(NONE);
    update_last_tick_chord();

    Serial.println("Finished open_all_strings()");
}

// All the modifiers change the chord in place
void make_sus2(int chord[]) {
    chord[1] = (chord[0] + 2) % 12;
}
void make_minor(int chord[]) {
    chord[1] = (chord[0] + 3) % 12;
}
void make_major(int chord[]) {
    chord[1] = (chord[0] + 4) % 12;
    chord[2] = (chord[0] + 7) % 12;
}
void swap_major_minor(int chord[]) {
    if (is_major(chord)) {
        make_minor(chord);
    } else {
        make_major(chord);
    }
}
void make_sus4(int chord[]) {
    chord[1] = (chord[0] + 5) % 12;
}
void make_dim(int chord[]) {
    chord[1] = (chord[0] + 3) % 12;
    chord[2] = (chord[0] + 6) % 12;
}
void make_aug(int chord[]) {
    chord[1] = (chord[0] + 4) % 12;
    chord[2] = (chord[0] + 8) % 12;
}
void add_dim7(int chord[]) {
    chord[3] = (chord[0] + 9) % 12;
}
void add_min7(int chord[]) {
    chord[3] = (chord[0] + 10) % 12;
}
void add_maj7(int chord[]) {
    chord[3] = (chord[0] + 11) % 12;
}
void add_maj2(int chord[]) {
    chord[4] = (chord[0] + 14) % 12;
}

bool set_solenoid_power(const int amount) {
  analogWrite(PWM_POWER_PIN, amount);
}

void update_pin_states() {
    // Pins are low until we see them high
    for (int j=0; j< ROW_PIN_COUNT; j++) {
        for (int i=0; i< COL_PIN_COUNT; i++) {
          pin_states[i][j] = 0;
        }
    }

    // Save all the pin states
    for (int i=0; i< COL_PIN_COUNT; i++) {
        pinMode(COL_PIN_NUMBERS[i], OUTPUT);
        digitalWrite(COL_PIN_NUMBERS[i], LOW);
        for (int j=0; j< ROW_PIN_COUNT; j++) {
          if (digitalRead(ROW_PIN_NUMBERS[j]) == LOW) {
            pin_states[i][j] = 1;
          }
        }
        digitalWrite(COL_PIN_NUMBERS[i], HIGH);
        pinMode(COL_PIN_NUMBERS[i], INPUT);
    }
   /* Serial.println();
     // Print the pressed button array
    for (int j=0; j< ROW_PIN_COUNT; j++) {
        for (int i=0; i< COL_PIN_COUNT; i++) {
            Serial.print(is_pressed(i, j));
        }
        Serial.println();
    }
    Serial.println();*/
}

bool is_pressed(int row, int col) {
    if (KEYPAD_FLIP_VERTICAL) {
      row = 3 - row;
    }
    if (KEYPAD_FLIP_HORIZONTAL) {
      col = 3 - col;
    }
    return pin_states[row][col];
}

void setup() {
    delay(100);
    Serial.begin(9600);
    Serial.println("Setting up pins...");
    setPwmFrequency(PWM_POWER_PIN, 1);
    for (int i=0; i< COL_PIN_COUNT; i++) {
        pinMode(COL_PIN_NUMBERS[i], OUTPUT);
    }
    for (int i=0; i< ROW_PIN_COUNT; i++) {
        pinMode(ROW_PIN_NUMBERS[i], INPUT_PULLUP);
    }

    pinMode(LATCH_PIN, OUTPUT);
    pinMode(DATA_PIN, OUTPUT);
    pinMode(CLOCK_PIN, OUTPUT);

    set_solenoid_power(current_power);
    set_current_chord(NONE);
    actuate_current_chord();
    update_last_tick_chord();

    Serial.println("Finished with setup()");
}

int get_col_state(int col) {
    int sum = 0;
    for (int r=0; r<ROW_PIN_COUNT; r++) {
        if (is_pressed(col,r)) {
            int power = ROW_PIN_COUNT - r - 1;
            sum += 1<<power;
        }
    }
    return sum;
}

int only_keep_rightmost_bit(int num) {
    for (int i=0; i<=7; i--) {
        if (1<<i & num)
            return 1<<i;
    }
}

int only_keep_leftmost_bit(int num) {
    for (int i=7; i>=0; i--) {
        if (1<<i & num)
            return 1<<i;
    }
}

void loop() {
    delay(TICK_DURATION);
    tick_counter += 1;
    update_pin_states();

    // is_pressed(c, r) key:
    //
    //       |_  col3  _|_  col2  _|_   col1  _|_  col0  _|
    // row0: |_ (0,3)  _|_ (0,2)  _|_  (0,1)  _|_ (0,0)  _|
    // row1: |_ (1,3)  _|_ (1,2) __|__ (1,1)  _|_ (1,0) __|
    // row2: |_ (2,3)  _|_ (2,2)  _|_  (2,1)  _|_ (2,0)  _|
    // row3: |__(3,3)  _|_ (3,2) __|__ (3,1)  _|_ (3,0) __|

    // Exhaustive chord layout 16 button edition
    //
    // Single press / double modifier as actuator (horizontal):
    //
    //       |_  col3  _|_  col2  _|_   col1  _|_  col0  _|
    // row0: |_  VIIb  _|_  IV    _|_   I     _|_  V     _|
    // row1: |__ ii    _|_  vi   __|__  iii   _|_  vii° __|
    // row2: |__       IV#       __|__        IIIb      __|
    // row3: |__       I#        __|__        VIb       __|
    //
    // Double press as actuator (adjacent fifths):
    //
    //       |_  col3  _|_  col2  _|_   col1  _|_  col0  _|
    // row0: |_        IV7        _|_          V7        _|
    // row1: |__       VI7       __|__        VII7    ° __|
    // row2: |__                 __|__                  __|
    // row3: |__                 __|__                  __|
    //
    // (cont.)
    //
    //       |_  col3  _|_  col2  _|_   col1  _|_  col0  _|
    // row0: |_        _|_         I7         _|_    II7
    // row1:   II7     _|_        III7        _|_       __|
    // row2: |__                 __|__                  __|
    // row3: |__                 __|__                  __|
    //
    // Double modifier as actuator (horizontal):
    //
    //       |_  col3  _|_  col2  _|_   col1  _|_  col0  _|
    // row0: |_                                          _|
    // row1: |_       ______                ______       _|
    // row2:  _Autoplay_|__      NONE        __|_Autoplay_ 
    // row3: |_         |__      PREV        __|         _|
    //
    // Single modifiers for single presses
    //
    //       |_  col3  _|_  col2  _|_   col1  _|_  col0  _|
    // row0: |_                                          _|
    // row1: |__       ___        ___         ___        _|
    // row2: |_ Make Do_|_  Add2  _|_  Sus4   _|_ Maj/min_|
    // row3: |_  mM7   _|_  MM7   _|_  mm7    _|_  Mm7   _|

    // Double modifiers for single presses (vertical combo):
    //
    //       |_  col3  _|_  col2  _|_   col1  _|_  col0  _|
    // row0: |_                                          _|
    // row1: |__       ___        ___         ___        _|
    // row2: |   Dim    |   Aug    |   Dim7    | 1/2 Dim7 |
    // row3: |_        _|_        _|_         _|_        _|

    bool check_modifiers = false;
    // Double presses
    if (is_pressed(0,0) && is_pressed(1,0)) {
        set_current_chord_in_current_key(V);
        make_major(current_chord);
        add_min7(current_chord);
    } else if (is_pressed(1,0) && is_pressed(2,0)) {
        set_current_chord_in_current_key(I);
        make_major(current_chord);
        add_min7(current_chord);
    } else if (is_pressed(2,0) && is_pressed(3,0)) {
        set_current_chord_in_current_key(IV);
        make_major(current_chord);
        add_min7(current_chord);
    } else if (is_pressed(0,1) && is_pressed(1,1)) {
        set_current_chord_in_current_key(VII);
        make_major(current_chord);
        add_min7(current_chord);
    } else if (is_pressed(1,1) && is_pressed(2,1)) {
        set_current_chord_in_current_key(III);
        make_major(current_chord);
        add_min7(current_chord);
    } else if (is_pressed(2,1) && is_pressed(3,1)) {
        set_current_chord_in_current_key(VI);
        make_major(current_chord);
        add_min7(current_chord);
    } else if (is_pressed(3,1) && is_pressed(0,0)) {
        set_current_chord_in_current_key(II);
        make_major(current_chord);
        add_min7(current_chord);
    // Single presses (possible modifiers)
    } else if (is_pressed(0,0)) {
        set_current_chord_in_current_key(V);
        make_major(current_chord);
        check_modifiers = true;
    } else if (is_pressed(1,0)) {
        set_current_chord_in_current_key(I);
        make_major(current_chord);
        check_modifiers = true;
    } else if (is_pressed(2,0)) {
        set_current_chord_in_current_key(IV);
        make_major(current_chord);
        check_modifiers = true;
    } else if (is_pressed(3,0)) {
        set_current_chord_in_current_key(VIIb);
        make_major(current_chord);
        check_modifiers = true;
    } else if (is_pressed(0,1)) {
        set_current_chord_in_current_key(VII);
        make_dim(current_chord);
        check_modifiers = true;
    } else if (is_pressed(1,1)) {
        set_current_chord_in_current_key(III);
        make_minor(current_chord);
        check_modifiers = true;
    } else if (is_pressed(2,1)) {
        set_current_chord_in_current_key(VI);
        make_minor(current_chord);
        check_modifiers = true;
    } else if (is_pressed(3,1)) {
        set_current_chord_in_current_key(II);
        make_minor(current_chord);
        check_modifiers = true;
    // Double modifier as actuator
    } else if (is_pressed(0,2) && is_pressed(1,2)) {
        set_current_chord_in_current_key(IIIb);
        make_major(current_chord);
    } else if (is_pressed(0,3) && is_pressed(1,3)) {
        set_current_chord_in_current_key(VIb);
        make_major(current_chord);
    } else if (is_pressed(2,2) && is_pressed(3,2)) {
        set_current_chord_in_current_key(IVsharp);
        make_major(current_chord);
    } else if (is_pressed(2,3) && is_pressed(3,3)) {
        set_current_chord_in_current_key(Isharp);
        make_major(current_chord);
    } else if (is_pressed(1,2) && is_pressed(2,2)) {
        set_current_chord(NONE);
    } else if (is_pressed(0,2) && is_pressed(3,2)) {
        if (tick_counter - last_onpress_action > TICKS_BETWEEN_ONPRESS_ACTIONS) {
            Serial.print("Toggling auto_play");
            auto_play = !auto_play;
        }
        last_onpress_action = tick_counter;
        set_current_chord(last_tick_chord); // Use of the change key button means no change in chord
    } else if (is_pressed(1,3) && is_pressed(2,3)) {
        if (tick_counter - last_onpress_action > TICKS_BETWEEN_ONPRESS_ACTIONS) {
            set_current_chord(prev_chord);
        }
        last_onpress_action = tick_counter;
    }

    if (check_modifiers) {
        if (is_pressed(0,2) && is_pressed(0,3)) {
            make_dim(current_chord);
            add_min7(current_chord);
        } else if (is_pressed(1,2) && is_pressed(1,3)) {
            make_dim(current_chord);
            add_dim7(current_chord);
        } else if (is_pressed(2,2) && is_pressed(2,3)) {
            make_aug(current_chord);
        } else if (is_pressed(3,2) && is_pressed(3,3)) {
            make_dim(current_chord);
        } else if (is_pressed(0,2)) {
            swap_major_minor(current_chord);
        } else if (is_pressed(1,2)) {
            make_sus4(current_chord);
        } else if (is_pressed(2,2)) {
            add_maj2(current_chord);
        } else if (is_pressed(0,3)) {
            make_major(current_chord);
            add_min7(current_chord);
        } else if (is_pressed(1,3)) {
            make_minor(current_chord);
            add_min7(current_chord);
        } else if (is_pressed(2,3)) {
            make_major(current_chord);
            add_maj7(current_chord);
        } else if (is_pressed(3,3)) {
            make_minor(current_chord);
            add_maj7(current_chord);
        } else if (is_pressed(3,2)) {
            if (tick_counter - last_onpress_action > TICKS_BETWEEN_ONPRESS_ACTIONS) {
                Serial.print("Changing key to: ");
                Serial.print(notes[current_chord[0]]);
                current_key = current_chord[0] % 12;
            }
            last_onpress_action = tick_counter;
            set_current_chord(last_tick_chord); // Use of the change key button means no change in chord
        }
    }

    if (is_same_chord(current_chord, last_tick_chord)) {
      if (tick_counter - last_chord_change_tick > TICKS_AT_FULL_POWER) {
        if (current_power != MID_POWER && !is_same_chord(current_chord, NONE)) {
          Serial.println("Setting MID_POWER");
          current_power = MID_POWER;
          set_solenoid_power(current_power);
        }
      }
    } else {
        last_chord_change_tick = tick_counter;

        // Since current_chord does not equal last_tick_chord, we want to store
        // last_tick_chord as the new prev_chord
        update_prev_chord();

        Serial.print(tick_counter);
        Serial.print(" ");
        for (int n=0; n<4; n++) {
            if (current_chord[n] >= 0) {
                Serial.print(notes[current_chord[n]]);
                Serial.print(" ");
            }
        }
        Serial.println();

        // It seems to be very important that we are set to full power (0 PWM
        // cycle) during the chord change. Otherwise, sometimes when we call
        // actuate_current_chord(), the 8 bit shift registers will get the
        // wrong data somehow.
        current_power = FULL_POWER;
        set_solenoid_power(current_power);

        actuate_current_chord();
        Serial.println("Set current chord");
        update_last_tick_chord();

        if (auto_play) {
          set_solenoid_power(NO_POWER);
          delay(20);
          set_solenoid_power(FULL_POWER);
        }
    }
}
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

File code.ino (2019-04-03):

int current_key = 0; // The key the instrument is currently in, with C being 0

void change_key_by(int half_steps) {
    current_key = current_key + half_steps % 12;
{

// Just the basic chords. Modifiers, including minor should all be applied as functions
// -1 indicates no note
/*const Chord triad_list[] = {
    {"IV", {5, 9, 0, -1}},
    {"I", {0, 4, 7, -1}},
    {"V", {7, 11, 2, -1}},
    {"II", {2, 6, 9, -1}},
    {"VI", {9, 1, 4, -1}},
    {"III", {4, 8, 11, -1}},
    {"VII", {11, 3, 6, -1}},
};*/

/* Key agnostic chord */
/*typedef struct {
    String name;
    int scale_degrees[];
} Chord */

const int IV[] = {5, 9, 0, -1};
const int I[] = {0, 4, 7, -1};
const int V[] = {7, 11, 2, -1};
const int II[] = {2, 6, 9, -1};
const int VI[] = {9, 1, 4, -1};
const int III[] = {4, 8, 11, -1};
const int VII[] = {11, 3, 6, -1};
int current_chord[] = {-1, -1, -1, -1};

// Copy the specified triad into the current_chord
void set_current_chord(int[] triad) {
    current_chord[0] = (triad[0] + current_key) % 12;
    current_chord[1] = (triad[1] + current_key) % 12;
    current_chord[2] = (triad[2] + current_key) % 12;
    current_chord[3] = (triad[3] + current_key) % 12;
}

// All the modifiers, change the chord in place
void make_sus2(int[] chord) {
    chord[1] = (chord[0] + 2) % 12;
    //chord.name = String(chord.name + "_sus2")
}
void make_minor(int[] chord) {
    chord[1] = (chord[0] + 3) % 12;
    //chord.name = String(chord.name + "_min")
}
void make_major(int[] chord) {
    chord[1] = (chord[0] + 4) % 12;
    //chord.name = String(chord.name + "_maj")
}
void make_sus4(int[] chord) {
    chord[1] = (chord[0] + 5) % 12;
    //chord.name = String(chord.name + "_sus4")
}
void make_dim(int[] chord) {
    chord[1] = (chord[0] + 3) % 12;
    chord[2] = (chord[0] + 6) % 12;
    //chord.name = String(chord.name + "_dim")
}
void make_aug(int[] chord) {
    chord[1] = (chord[0] + 4) % 12;
    chord[2] = (chord[0] + 8) % 12;
    //chord.name = String(chord.name + "_aug")
}
void add_dim7(int[] chord) {
    chord[3] = (chord[0] + 9) % 12;
    //chord.name = String(chord.name + "_dim7")
}
void add_min7(int[] chord) {
    chord[3] = (chord[0] + 10) % 12;
    //chord.name = String(chord.name + "_min7")
}
void add_maj7(int[] chord) {
    chord[3] = (chord[0] + 11) % 12;
    //chord.name = String(chord.name + "_maj7")
}


const int[] col_pin_numbers = { -1, -1, -1 };
const int[] col_pin_states   = { -1, -1, -1 };
const int[] row_pin_numbers = { -1, -1, -1, -1 };
const int[] row_pin_states   = { -1, -1, -1, -1 };

void setup() {
    Serial.begin(9600);
    for (int i=0; i< sizeof(col_pin_numbers); i++) {
        pinMode(col_pin_numbers[i], INPUT_PULLUP);
    }
    for (int i=0; i< sizeof(row_pin_numbers); i++) {
        pinMode(row_pin_numbers[i], INPUT_PULLUP);
    }
}

void loop() {

    // Read all the pins once
    for (int i=0; i< sizeof(col_pin_numbers); i++) {
        col_pin_states[i] = digitalRead(col_pin_numbers[i])
    }
    for (int i=0; i< sizeof(row_pin_numbers); i++) {
        row_pin_states[i] = digitalRead(row_pin_numbers[i])
    }

    // Debug print the buttons pushed
    for (int r=0; r< sizeof(row_pin_states); r++) {
        for (int c=0; c< sizeof(col_pin_states); c++) {
            if (row_pin_states[r] == LOW && col_pin_states[c] == LOW) {
                Serial.print("1")
            } else {
                Serial.print("0")
            }
        }
    }
}

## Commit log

2019-04-01 Remove current-section header
2019-04-02 Add 12 button layouts
2019-04-04 Get basic chord logic framework
2019-04-04 Fill in all the button/chord logic
2019-04-05 Get note output for all chords correct
    [code.ino]
2019-04-05 Fix indentation
    Using vim 4 space = 1 tab
    [code.ino]
2019-04-09 Adding Fritzing breadboard diagram file and jpg
    [smart-o-harp.fzz]
2019-04-19 Update diagram, add components
    [smart-o-harp.fzz]
2020-01-14 Massive changes for 2nd construction
    I started over building because the first build was cludgy and bad in
    its unfinished state. Here are the major changes in the second
    construction, in hardware and software:
    - Using 16 button keypad (4 column, 4 row pins, no weird ground pin
    this time ;) This causes:
    - Different button reading strategy: Use two dimensional array of
    button states rather than row and column states. This allows a lot more
    keypresses without ambiguity.
    - Keymapping to chords substantially rethought. Now it doesn't use ANY
    simultaneous keypresses, but considers some keys as "modifiers" which
    don't do anything when pressed on their own, and "actuators" (maybe
    find bett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
    [code.ino]
2020-01-22 Make solenoid pin order more explicit
2020-01-23 Step up and down from full and low power
2020-01-24 Solve all unpredictability issues ;)
    It seems to be very important that we are set to full power (0 PWM
    cycle) during the chord change. Otherwise, sometimes when we call
    actuate_current_chord(), the 8 bit shift registers will get the wrong
    data somehow. This was the original software setup, which I thought
    wasn't working originally.
    FULL_POWER doesn't have to be on for all that long, only between 25-50
    ms, then it can go immediately to LOW_POWER. Keeping this time low seems
    to help the power supply/capacitor keep up.
    Here's all the possible things that I can think of that may have also
    been important
    - I added a big 220uF capacitor across the power source, though
    removing it doesn't see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
    [code.ino]
2020-01-26 Replace sus2 with dom9
    Get rid of sus2 from the keypad entirely. The motivation is that IVsus2
    = Isus4, Isus2 = Vsus4, etc. around the circle of 5ths. Furthermore,
    after playing around with it there doesn't seem to be a huge auditory
    difference.
    The choice to move dom9 to the new spot is that I want to try it out
    more and it was the only modifier using a double diagonal modifier
    combo.
    [code.ino]
2020-01-26 Add a NONE chord combo. Feeble attempt at ALL
    The NONE chord is now playable, which just dampens all strings, which is
    the same state the instrument starts in. Pretty basic stuff.
    The ALL chord is more tricky. Raising every solenoid at once is a huge
    power draw, and only sometimes works, pulling the voltage unacceptably
    low and sometimes resetting the arduino. Perhaps I should try a simpler
    solution; this added function may be too complex. In any case, I
    decided not to assign the function on the keypad.
    [code.ino]
2020-02-01 Untested: Make double actuators more "circle-of-fifths-ish"
    We currently had the VIb and IIIb as near-the-key triads, playable using
    a double modifier combo. Having encountered a need for the IV# (major
    sharp IV) I realized that by adding just that and I#, we could have
    playable chords built on all 12 semitones, if not flexibility of
    tonality for 4 of them.
    The right-side double modifiers represent going out the key in the
    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
2020-02-01 Untested: Change out prev for last_tick
    This find and replace will help be less ambiguous for if I decide to add
    in a "Previous chord" action that will go back to the chord before the
    currently actuated chord.
    [code.ino]
2020-02-01 Make the keypad layout diagram much nicer and correcter
    [code.ino]
2020-02-01 Untested: Add PREV functionality
    A press of the PREV button combination will cause the instrument to "go
    back a chord", in other words, change chords to the most recent chord
    played that is different from the current_chord.
2020-10-01 Revise for 7V power, and add constants for keypad flips
    [code.ino]
2022-06-17 Pull kicad files into repo
    [smart-o-harp-B_Cu.gbl, smart-o-harp-B_Mask.gbs, smart-o-harp-B_SilkS.gbo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]
